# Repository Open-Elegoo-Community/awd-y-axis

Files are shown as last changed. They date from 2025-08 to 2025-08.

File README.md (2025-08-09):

# AWD Y Axis
Status: Complete - Documentation is in progress

## Proposal
The Y axis is underpowered. In comparison to the X axis, it is almost twice as slow in acceleration. This is due to having almost three times the load. Using multiple motors is not new and has been showcased successfully with other bed slingers, most notably the LH Stinger.

I propose to add an additional motor to the Y-axis by using Layer.shifted [Neptune 4/4pro Y-Axis Double Shear 9mm Belt Upgrade](https://www.printables.com/model/1208536-neptune-44pro-y-axis-double-shear-9mm-belt-upgrade) and mounting it in place of the Y-axis tensioner.

This modification also requires a new tensioner design and a way to automatically sync the two motors.

## Prerequists
The first order of business is to print, source, and build out The Y-Axis Double Shear. Once this is stable, then proceed to the next step. Remember to keep as much length of the belt as possible, you will need it when the additional motor is added.

### BOM
| QTY |  Item |
|-----|---|
| 4 | M3 hex nuts (square should work too) |
| 4 | M3 x 40 hex sockethead cap screws |
| 1 | Mellow FLY adxl345 |
| 1 | USB cable (maybe 1 meter) |
| 2 | M3 x D5.0 x L4.0 heat inserts |
| 2 | M3 x 5 button or cap screws |
| 4 | M4 x 15 (I think) button head screws |

## Tensioner
Building the tensioner should be the second priority. My first iterations were printed from PETG, but after a few months, I found that it deformed badly under the pressure of the base plate mounting screws, and the belt retainers did. After redesigning the tensioner system to be more compact and include a spot for an adxl345, I printed this in ASA-CF. So far, it is holding just fine.

PETG Trials (pre adxl):



ASA-CF (with Mellow Fly adxl345)


ASA (with Mellow Fly adxl345) - Updated


## Second Motor
You need to add a MKS TMC2209 Stepper Motor Driver to the spare socket on your mainboard. Make sure to add the jumper to enable UART.
Adding the second motor is as simple as installing the first. 
- Bolt on the new Y tensioner to the bed
- Remove the stock Y tensioner, and mount the new motor using the same instructions.
- Find a suitable route for the motor wires and plug them into the driver pins.

## Adding Tension
There is a fore-and-aft tension system. 
- First, install the aft tensioner and install the screws so they grip onto the retaining nuts.
- Then install the front tensioner. Leave enough slack so you can start the screws into the retaining nuts.
- Slowly tighten the aft tensioner until there is 2mm of space. Then tighten the fore until you reach the desired frequency.

## Syncing the Motors
Syncing the motors is essential. If you do not the Input Shaping is unpredictable, and your steps will wear out faster as they play tug-of-war. You can either sync manually or automatically. Both ways work, however, the automatic way is slightly better.
- The manual approach is best described in the [LH Stinger documentation](https://github.com/lhndo/LH-Stinger/wiki/Tuning#awd-y-stepper-motor-sync).
- The automatic approach requires a dedicated adxl to be installed in the center of the base plate. I have used this [klipper plugin](https://github.com/MRX8024/motors-sync/tree/main) to accomplish the task of syncing. This guidance has been proven by the Voron core XY community.

## When to Sync the Motors
- You always need to sync the motors when you adjust the tension on the belt. Period. 
- With the automatic sync, you should also sync as part of your PRINT_START, because it's lazier to add it than to wonder if you should have added it.

## Tests
If I recall the dates correctly, I have the following

Single Y double shear


AWD manual sync


AWD adxl sync + rigid spacers


## Talk throughs
- [Part 1](https://www.youtube.com/shorts/GpRsdIZC7Hs)
- [Part 2](https://youtube.com/shorts/7Iwm1x9LCUw)
- [Part 3](https://youtube.com/shorts/XBzKG74UmCE)
- [Part 4](https://youtube.com/shorts/STW_UA8tv80)
- [Part 5](https://youtu.be/CL45KMCeoP4)

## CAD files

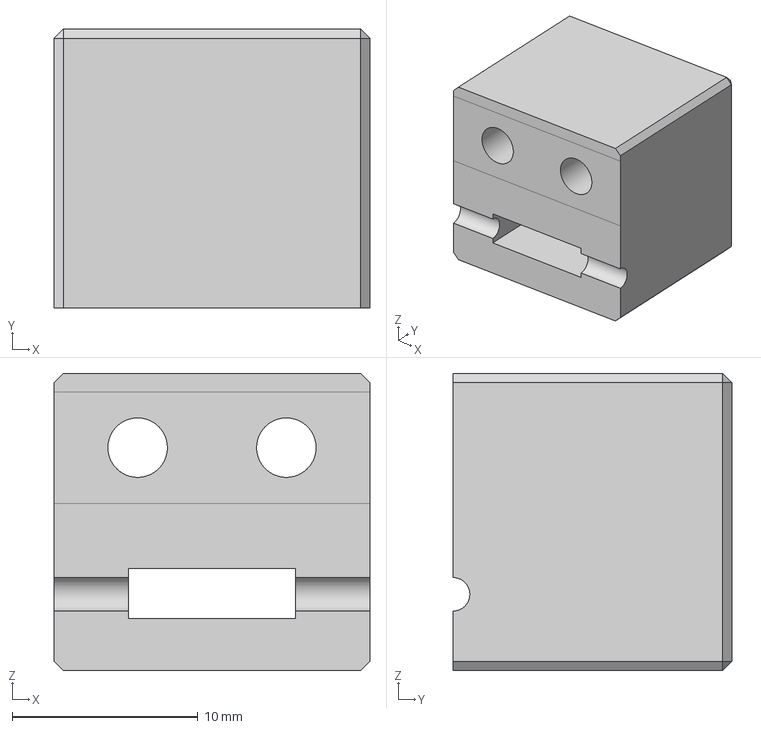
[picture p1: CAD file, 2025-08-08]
step-files/tensioner.step
17.0 x 15.0 x 16.0 mm

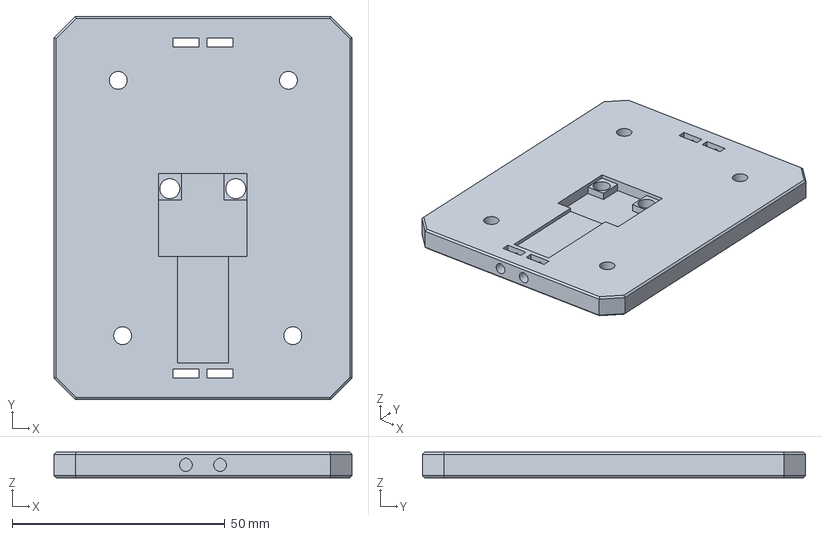
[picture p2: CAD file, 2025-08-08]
step-files/tensioner-plate.step
70.0 x 90.0 x 6.00 mm

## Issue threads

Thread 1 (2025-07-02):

Cad files missing

Faf101290, 2025-07-02:
There's no cad files for the center carriage and tensionner

dvystrcil, 2025-08-08:
The step files have been uploaded.

Closed 2025-08-08.
